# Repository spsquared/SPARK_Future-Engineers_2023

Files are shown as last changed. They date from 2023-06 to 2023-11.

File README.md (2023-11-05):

<div align=center>

banner

</div>

***

**Official GitHub repository for WRO USA Future Engineers team SPARK 2023. All code, documentation, and files are located here.**

***

# Contents
* [**Hardware Design**](#hardware-design)
    * [Chassis](#chassis)
    * [Power & Control](#power--control)
    * [Motors](#motors)
    * [Sensors](#sensors)
    * [Wiring Diagram](#wiring-diagram)
* [**Software Design**](#software-design)
* [**Photos**](#photos)
* [**In-depth Algorithm Documentation**](ALGORITHM.md)
* [**Build & Setup**](#build--setup)
    * [Parts List](#parts-list)
    * [Important Assembly Notes](#important-assembly-notes)
    * [Jetson Nano Setup](#jetson-nano-setup)
        * [General Information](#general-jetson-nano-information)
        * [OS Installation](#os-installation)
        * [SSHFS & Static IP](#sshfs--static-ip)
        * [GPIO & I2C](#enable-gpio-and-i2c)
        * [Package Installation](#package-installation)
        * [Camera Profile Fix](#camera-profile-fix)
        * [Calibration](#calibration)
        * [Running Programs](#running-programs)
* [**Demonstration Videos**](#demonstration-videos)
* [**Team Photos**](#team-photos)
* [**SPARK Utilities**](#spark-utilities)
    * [SPARK Control Panel](#spark-control-panel)
        * [Map View](#map-view)
        * [Changing Parameters](#changing-parameters)
    * [SPARK Randomizer](#spark-randomizer)
    * [Setup](#spark-utility-setup)
* [**Lessons Learned**](#lessons-learned)
* [**LiPo Battery Safety Notice**](#lipo-battery-safety-notice)

***

# Hardware Design

SPARK G2 consists of a 3D-printed chassis with off-the-shelf components mounted to it, like motors, cameras, and controller boards. For a full component list, see [SETUP.md](./SETUP.md#parts-list). CAD models can be found in `/dist/3d-models/`, and have all been [modeled in Onshape here](https://cad.onshape.com/documents/82dd14d30b814e8846567203/w/34e1b6a4058ed5fbde8ef66a/e/47aa4028e09ec17a24a63590).

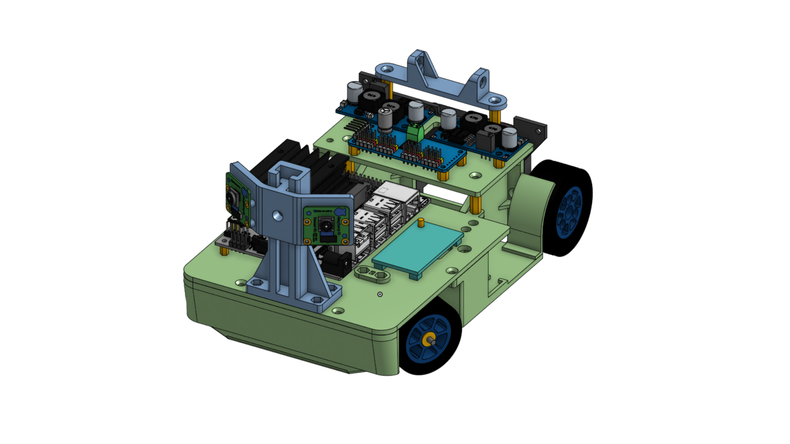
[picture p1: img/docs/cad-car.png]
SPARK G2 chassis with electronics in CAD software


***

## Chassis

The chassis consists of a lower base with vertical walls to mount the rear axle and upper platforms. It has space for the battery and ESC (electronic speed controller) bay in the rear, and a compartment in the front for the steering mechanism. The rear axle is sourced from the Atom 2 GT12 pan car kit by Schumacher and is mounted vertically to save space.

The electronics platforms sit on top of the chassis base, and the main platform is also a structural component that provides rigidity to the chassis. Because the electronics are on top, they are easily accessible and wiring is fairly simple. The only exceptions are the ESC, which is in the rear, and the IMU (inertial measurement unit, used for measuring angles and velocity).

| Chassis base with rear axle and steering | Chassis base and platforms, without camera tower |
| --- | --- |
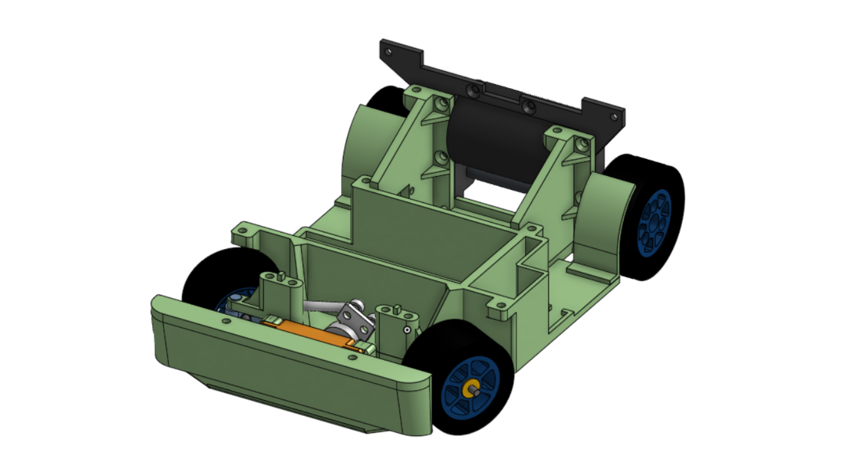
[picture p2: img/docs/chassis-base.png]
Lower chassis base
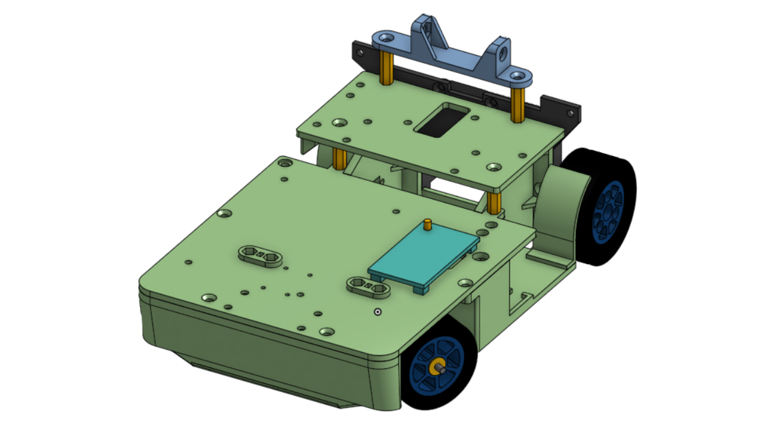
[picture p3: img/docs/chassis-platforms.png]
Chassis with platforms
|  |  |

The wheels are made of 3D-printed rims with LEGO tires, and the front steering linkage is a custom design with an exaggerated [Ackerman steering geometry](https://en.wikipedia.org/wiki/Ackermann_steering_geometry). (This can be seen in the [Motors section](#motors))

## Power & Control

The vehicle power is supplied by a single 3s LiPo battery, running at 12 Volts. This 12V power is run into three components in parallel: The ESC, 5V regulator, and 7.4V regulator. The regulators ensure that the Jetson Nano and servo do not get damaged from overvoltage, and the ESC can run directly off of the main 12V line.

The Jetson Nano uses an intermediate PWM control board to control the drive and steering motors. The control board and Nano communicate through I2C, and that is converted to a PWM signal for the motors to interpret. The drive motor has an additional speed controller.

| Top-down view of SPARK G2 in Onshape | Individual components |
| --- | --- |
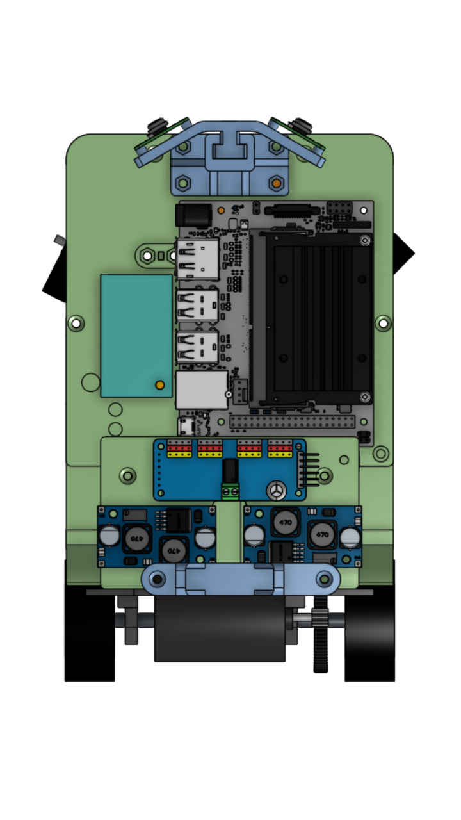
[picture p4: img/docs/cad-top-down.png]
Top-down in CAD
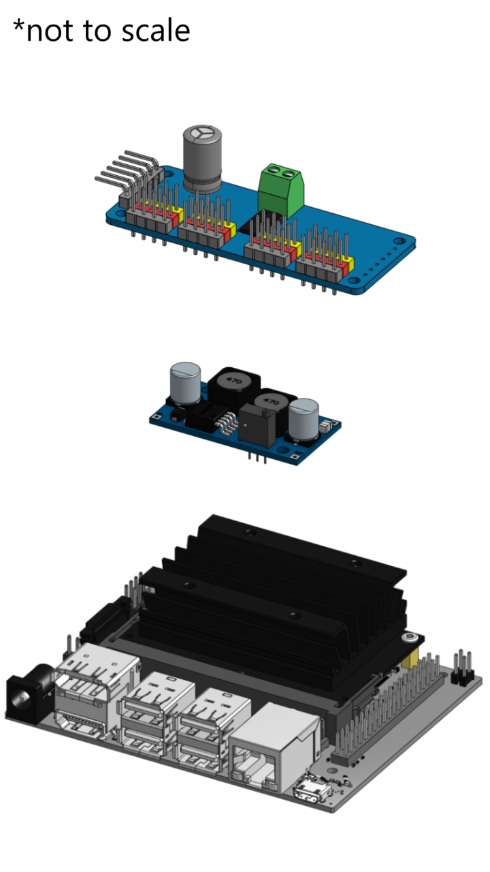
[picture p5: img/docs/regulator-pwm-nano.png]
Individual components
|  |  |
| Front of vehicle at top | (top-to-bottom) - PWM Driver, Voltage regulator, Jetson Nano |

## Motors

SPARK is rear-wheel drive, with a sensored brushless drive motor and high-quality servo from Savox. The drive motor is controlled by the brushless ESC (electronic speed controller) and has a sensor. Brushless motors allow for finer control at low speeds, and the addition of a sensor helps too.

It still would be better to use a lower kV motor (a slower motor) with an [ODrive](https://odriverobotics.com/) and encoder for even better low-speed control, but the current setup is sufficient.

We chose to use the Savox SV1260MG for our steering servo because of its speed - with transit times of under 100ms, this servo would not limit our control of the vehicle. It can also run at higher voltages, meaning we can get more power out of it.

| Drive motor | Servo and steering |
| --- | --- |
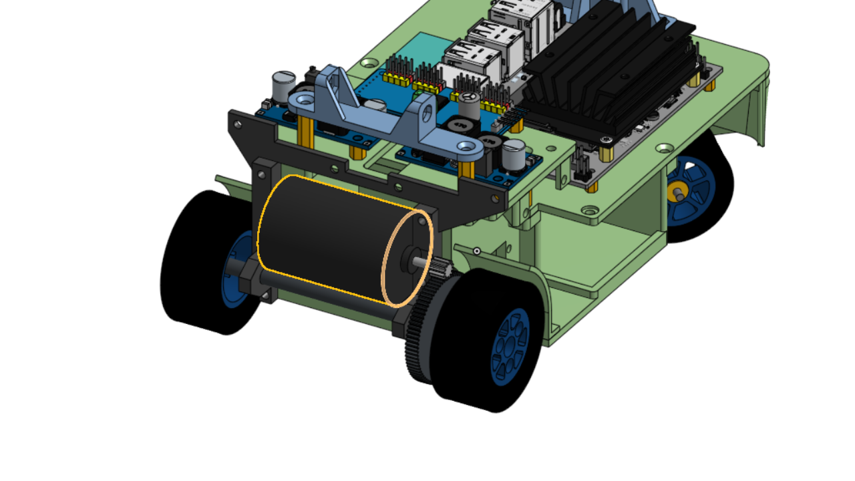
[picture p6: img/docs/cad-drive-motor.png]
Drive motor
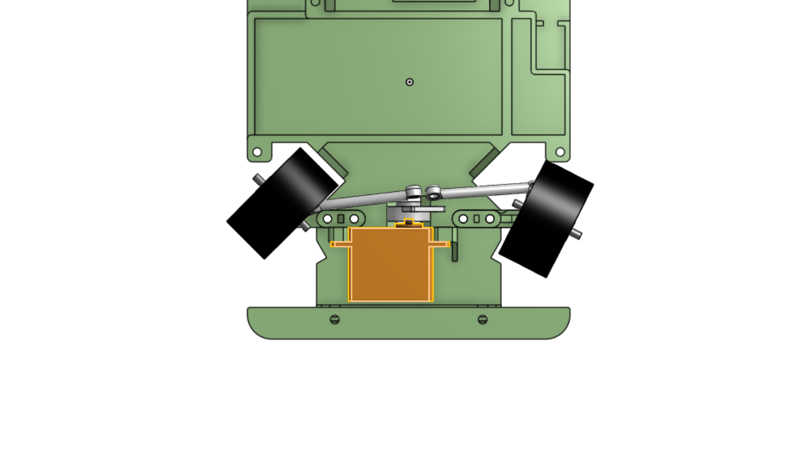
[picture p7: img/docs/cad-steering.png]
Servo and steering mechanism
|  |  |

## Sensors

One major physical change is the addition of a second IMX219 wide-angle camera to the front of the car. Both cameras are angled 30 degrees to either side, with a field of view of 150 degrees for each camera. The cameras are mounted on a slider to ensure the accuracy of the [distance calculations in the algorithm](./ALGORITHM.md#merge-contours--wall-lines).

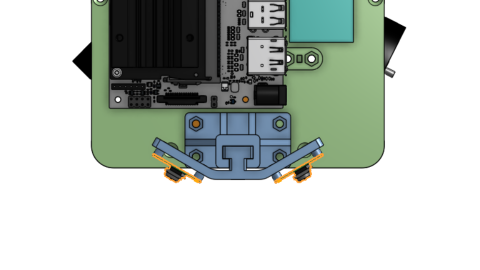
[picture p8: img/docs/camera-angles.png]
Cameras top-down


In addition to the two wide-angle cameras, SPARK G2 has an IMU (inertial measurement unit) for measuring the angle of the vehicle. It also has the capability to measure linear acceleration, but we don't use that. It communicates over I2C directly with the Jetson Nano.

SPARK G2 does not use any other sensors to perceive its environment - no LiDAR here!

## Wiring Diagram

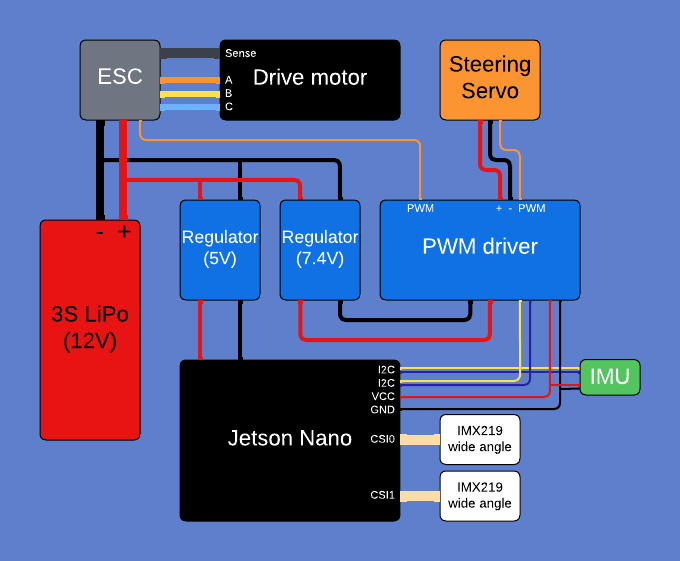
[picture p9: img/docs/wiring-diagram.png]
Wiring diagram


***

# Software Design

[**For a detailed explaination of the SPARK G2 algorithms, see Algorithm.md!**](ALGORITHM.md)

## [Obstacle Management Algorithm](ALGORITHM.md)

* [**Image Processing**](ALGORITHM.md#image-processing)
    1. [Crop the image](ALGORITHM.md#crop-the-image)
    2. [Undistort](ALGORITHM.md#undistorting)
    3. [Filter](ALGORITHM.md#filtering)
    4. [Find wall heights](ALGORITHM.md#finding-wall-heights)
    5. [Find contours](ALGORITHM.md#finding-contours)
    6. [Find wall lines](ALGORITHM.md#finding-wall-lines)
    7. [Merge & Convert wall lines and contours](ALGORITHM.md#merge-contours--wall-lines)
    8. [Categorize Walls](ALGORITHM.md#categorizing-walls)
    9. [Find Car Orientation](ALGORITHM.md#finding-car-orientation)
    10. [Filter Traffic Signals/Obstacles/Pillars/Game Objects](ALGORITHM.md#filtering-traffic-signals)
* [**Steering and Motion Planning**](ALGORITHM.md#steering-and-motion-planning)
    1. [Find Lap Direction](ALGORITHM.md#finding-lap-direction)
    2. [Calculate Steering](ALGORITHM.md#calculating-steering)

## Pseudo Code

The algorithm part of the code is a loop. Each iteration, it takes images, processes them, and then calculates a steering value.

Each iteration takes about 80ms.

```
while (sections entered != 24): # 24 sections means 3 laps.
    // Image processing for car localization
    Crop the images
    Undistort the images (how to add links to other files?)
    Filter the image
    Find wall heights
    Find contours
    Find wall lines
    Merge and Convert wall lines and contours
    Categorize Walls
    Find Car Orientation
    Filter Pillars
    <!--Car steering control-->
    Find lap direction
    Calculate Steering
```

***

# Photos

*(Click to view detail)*

| | |
| --- | --- |
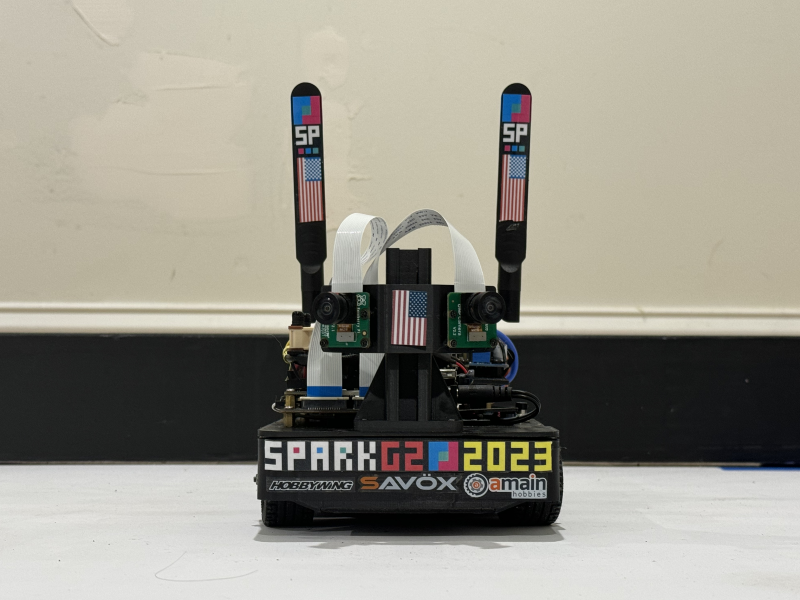
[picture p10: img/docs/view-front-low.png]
Front view
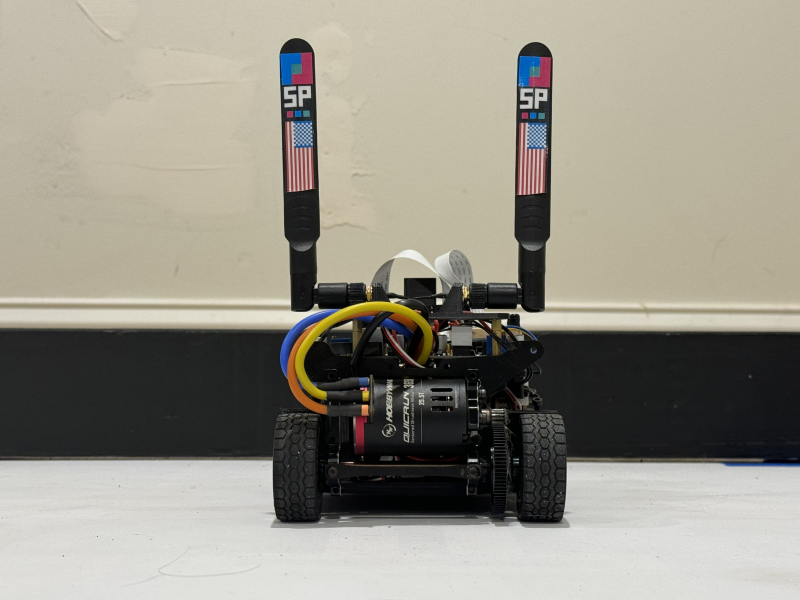
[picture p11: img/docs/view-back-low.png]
Back view
|  |  |
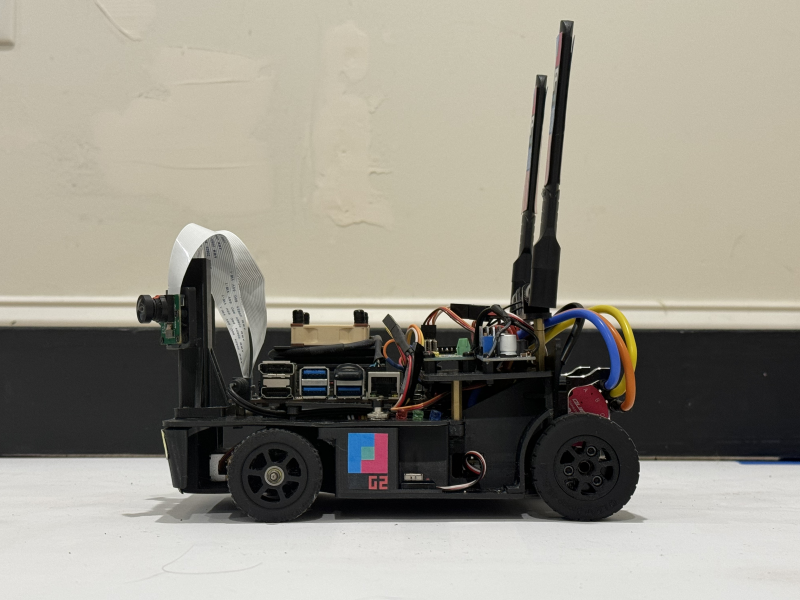
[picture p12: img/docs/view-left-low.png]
Side left view
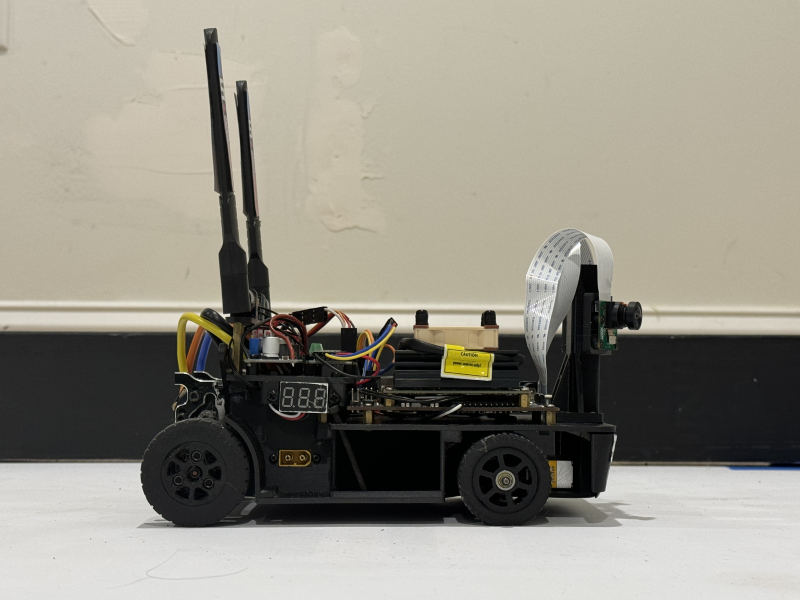
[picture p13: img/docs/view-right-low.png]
Side Right view
|  |  |
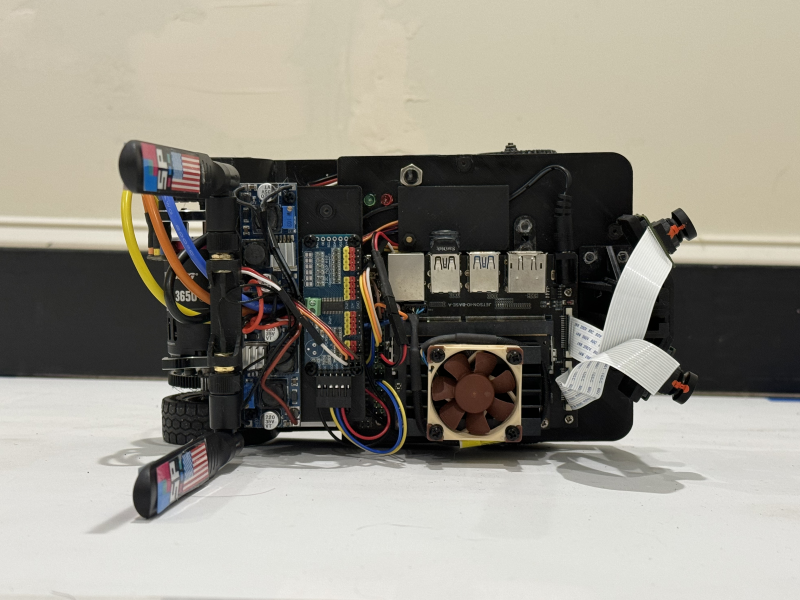
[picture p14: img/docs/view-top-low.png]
Top view
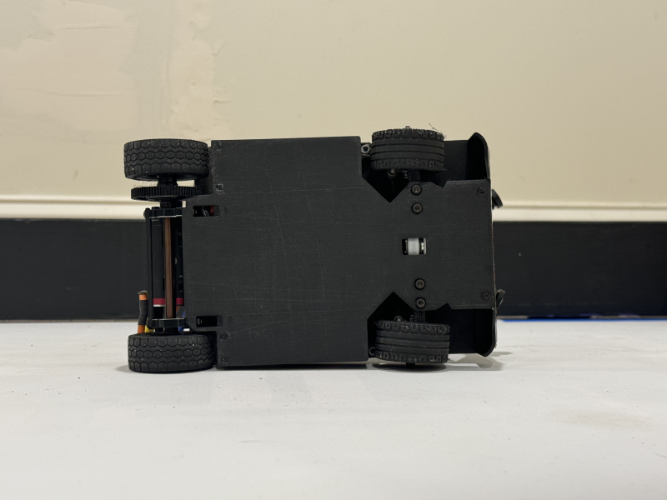
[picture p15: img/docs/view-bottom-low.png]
Bottom view
|  |  |

***

# Demonstration Videos

| Open Challenge | Obstacle Challenge (no U-turn) | Obstacle Challenge (U-turn) |
| --- | --- | --- |
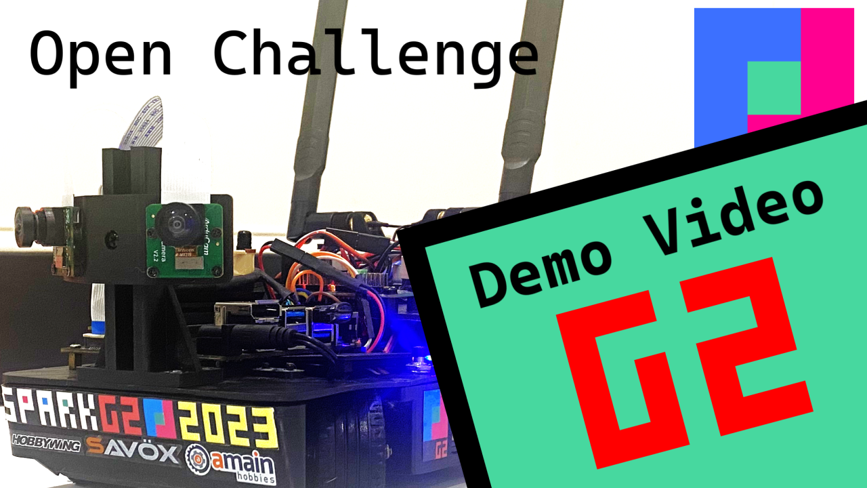
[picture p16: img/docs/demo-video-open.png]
SPARK WRO Future Engineers 2023 Internationals Demonstration Run - Open Challenge (https://youtu.be/1Tk8J1Zt5vI)
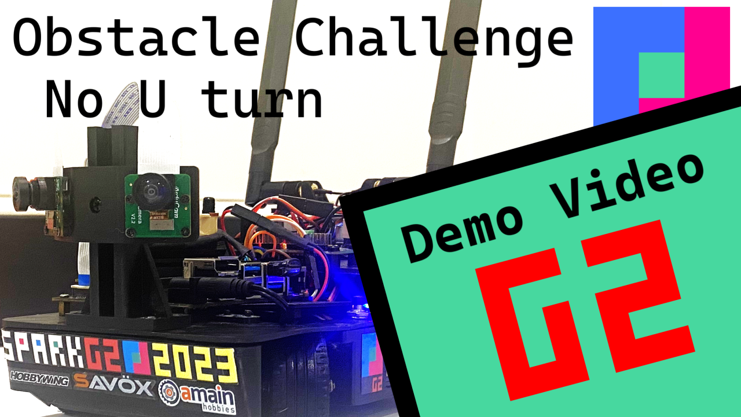
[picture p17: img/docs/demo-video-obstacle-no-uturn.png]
SPARK WRO Future Engineers 2023 Internationals Demonstration Run - Obstacle Challenge - No U turn (https://youtu.be/DUGlUvpnOEw)
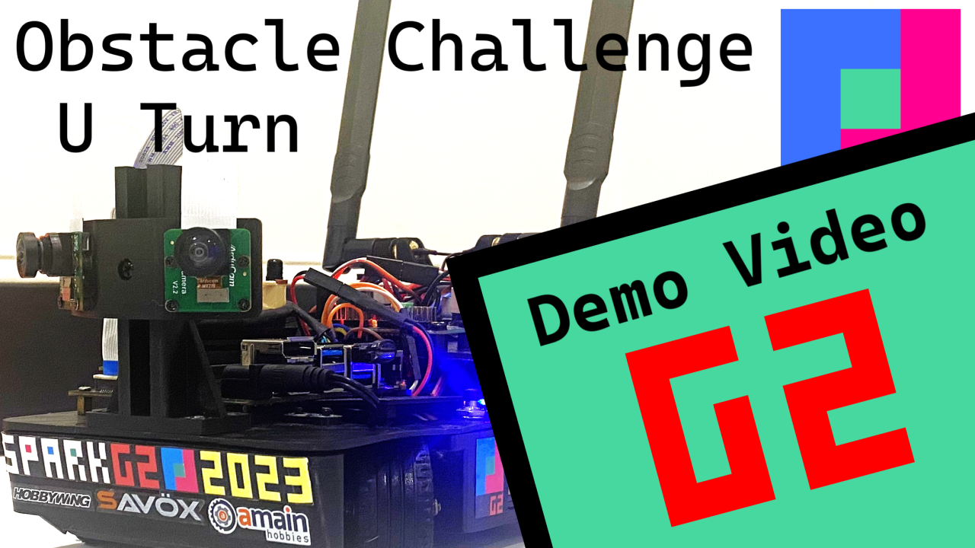
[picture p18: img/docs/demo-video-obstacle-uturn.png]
SPARK WRO Future Engineers 2023 Internationals Demonstration Run - Obstacle Challenge - U turn (https://youtu.be/UDNGXfyl8ww)
|  |  |  |

***

# Build & Setup

**This section is a walkthrough of the build process and setup of the controller, a Jetson Nano.**

***

You will need (at least) the following tools:
* 3D printer or access to 3D printing service
* Hex Allen drivers (key or bits)
* Phillips head drivers
* Crimping kit
* Soldering iron

***

## Parts:

* At least 0.8kg PLA filament
* Parts from [Schumacher Atom 2 S2 1/12 GT12 Competition Pan Car Kit](https://www.amainhobbies.com/schumacher-atom-2-s2-1-12-gt12-competition-pan-car-kit-schk179/p1055346) (not sponsored)
    * [Drive Pod Parts](https://www.racing-cars.com/gt12/atom-2/atom-2-parts=chassis-parts/s2-pod-parts-atom-2-u7905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)
    * [Assembled Differential](https://www.racing-cars.com/gt12/atom-2/atom-2-parts=transmission/assembled-diff-atom-2-u7713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)
    * [Left Drive Wheel Clamp](https://www.racing-cars.com/gt12/atom-2/atom-2-parts=transmission/lh-drive-clamp-a1-a2-u4853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)
    * Transmission Housings: [Left Side](https://www.racing-cars.com/gt12/atom-2/atom-2-parts=transmission/trans-housing-lh-a2-3-e2-e5-u7483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), [Right Side](https://www.racing-cars.com/gt12/atom-2/atom-2-parts=transmission/trans-housing-rh-a2-3-e2-e3-e4-u7484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)
    * [Ride Height Adjusters](https://www.racing-cars.com/gt12/atom-2/atom-2-parts=suspension/ride-height-adjusters-0-25-1-75-4prs-e1-5-ic-2-a3-u4973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) (use 1.75mm)
    * 2x [LP Front Axle](https://www.racing-cars.com/gt12/atom-2/atom-2-parts=suspension/low-profile-front-axle-a1-a3-u7302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)
    * [Rear Axle Ball Bearings](https://www.racing-cars.com/gt12/atom-2/ball-bearing-1-4x3-8x1-8-flanged-yellow-pr-u4980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)
    * [Front Axle Ball Bearings](https://www.racing-cars.com/gt12/atom-2/ball-bearing-1-8x5-16-flanged-yellow-pr-u4981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)
    * [Steel shims](https://www.racing-cars.com/gt12/atom-2/s-steel-shims-1-4x5-16x0-004-ss-at-ecl-u4112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)
    * [M3 Nyloc Nuts](https://www.racing-cars.com/gt12/atom-2/m3-alloy-nyloc-nuts-low-profile-black-pk10-cr517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)
    * [Servo Horn](https://www.racing-cars.com/gt12/atom-2/atom-2-parts=chassis-parts/25t-servo-saver-assembly-a2-e3-e4-u7895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)
    * [Ball Studs (short)](https://www.racing-cars.com/gt12/atom-2/pro-ball-stud-short-pk4-u4274?returnurl=%2fgt12%2fatom-2%2f)
* [Yahboom Jetson Nano 4GB Developer Kit](https://category.yahboom.net/collections/jetson/products/jetson-nano-sub)
* 2x [Arducam Raspberry Pi Official Camera Module V2, with 8 Megapixel IMX219 Wide Angle 175 Degree Replacement](https://www.amazon.com/Arducam-Raspberry-Official-Megapixel-Replacement/dp/B083PW4BLH/)
* [Intel AX201 WiFi 6 BT 5.1 M.2 2230 with 10in RP-SMA Antenna](https://www.newegg.com/p/0XM-009Y-001C7) (not required but helpful)
* [Noctua NF-A4x10 5V](https://noctua.at/en/products/fan/nf-a4x10-5v) (not required)
* [Adafruit MPU-6050 6-DoF Accelerometer & Gyroscope Sensor (with STEMMA QT connector)](https://www.adafruit.com/product/3886)
* [PCA9685 16 Channel PWM Driver](https://www.amazon.com/HiLetgo-PCA9685-Channel-12-Bit-Arduino/dp/B01D1D0CX2)
* [HobbyWing QUICRUN 10BL60 Brushless ESC Sensored](https://www.hobbywingdirect.com/products/quicrun-10-sensored)
* [HobbyWing QUICRUN 3650 Sensored Brushless Motor G2 (25.5T)](https://www.hobbywingdirect.com/collections/quicrun-brushless-motor-series-sensorless/products/quicrun-3650-sensored-2-pole-brushless-motor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)
* [Savox SV1260MG Digital Mini Servo](https://www.savoxusa.com/products/savsv1260mg-mini-digital-high-voltage)
* A LiPo balance charger with XT-60 connector, rated for 3S
* [Zeee Premium Series 3S LiPo Battery 4200mAh 11.4V 120C with XT60 Plug](https://www.amazon.com/Zeee-Premium-Compatible-Helicopter-Airplane/dp/B09CMLSK67)
* 2x [XL4015E1 DC-DC 5A Adjustable Buck Converter](https://www.amazon.com/Adjustable-Converter-1-25-36v-Efficiency-Regulator/dp/B079N9BFZC)
* [DC Digital Voltometer](https://www.amazon.com/bayite-Digital-Voltmeter-Display-Motorcycle/dp/B00YALUXH0/)
* [Male 5.5mm DC Barrel Connectors](https://www.amazon.com/Pigtails-Female-Connector-Pigtail-Security/dp/B08PYWN3T7/)
* [Panel-Mountable Female XT60 Connectors](https://www.amazon.com/XT60E-M-Mountable-Connector-Models-Multicopter/dp/B07YJMCDC3)
* [Normally Closed/Momentary On Push Button](https://www.amazon.com/Pieces-normally-closed-Button-Momentary/dp/B07HCLVMGS/) (size must match)
* [12 Tooth 48 Pitch Pinion Gear with Set Screw](https://www.amazon.com/Traxxas-PINION-PITCH-SCREW-2428/dp/B00EFXMUO2)
* [78 Tooth Spur Gear 48 Pitch](https://www.amazon.com/Kimbrough-Pitch-Spur-Gear-78T/dp/B0006O1QVM)
* 16, 20 gauge wire
* M3 nylon screws (6mm)
* M3 nylon standoffs (6mm works best)
* M3 nylon nuts
* M3 nuts
* Countersunk, cap head M3 screws (6mm and 8mm work best)
* Socket cap head M3x40mm screws [(like these)](https://www.amazon.com/Alloy-Steel-Socket-Screws-Black/dp/B00W97R5KU)
* Differential lubrication

## Important Assembly Notes

If you need a reference model we have our [OnShape document linked](https://cad.onshape.com/documents/82dd14d30b814e8846567203/w/34e1b6a4058ed5fbde8ef66a/e/47aa4028e09ec17a24a63590). (The ESC and IMU have not been modeled. The ESC goes in the rear, within the raised rectangle. The IMU should be mounted to the 4 unpopulated holes with M2.5 screws.)

### [**We HIGHLY recommend that you visit this document!**](https://cad.onshape.com/documents/82dd14d30b814e8846567203/w/34e1b6a4058ed5fbde8ef66a/e/47aa4028e09ec17a24a63590)

Follow the diagram below to wire the button and indicator LEDs. *(Click to view detail)*

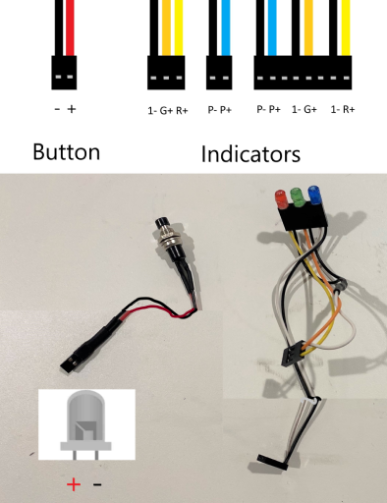
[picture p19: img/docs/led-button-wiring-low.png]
Button and indicator LED wiring


*Note: For I2C connectors, Yellow should be SCL, and blue should be SDA; there is no set standard.*

For soldering, we recommend soldering the regulators to their own connectors **in parallel**, and using that as a pass-through to the ESC. The female connectors should be used on the ESC inputs and regulator input, and the male connector on the pass-through end of the regulator wires. See the diagram below.

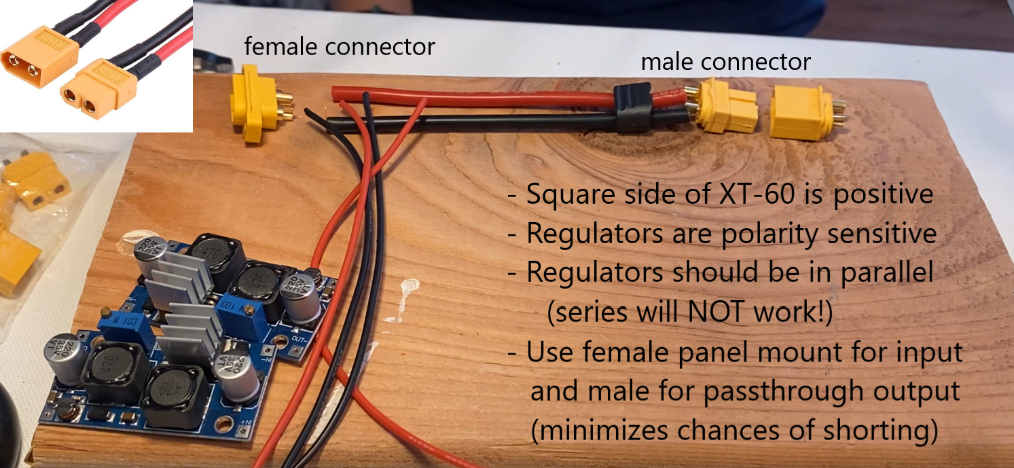
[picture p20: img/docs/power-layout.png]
Wiring for regulator passthrough


Follow the quick start guide for the ESC to solder the motor connections. Summary: solder A, B, and C connectors to the motor (or supplied connectors). Ensure the sensor wire is secure before mounting the motor and ESC.

**WARNING:** DO NOT CONNECT THE ESC 3-PIN DIRECTLY TO THE SERVO DRIVER! IT WILL BACKDRIVE THE REGULATOR AND BREAK IT! ONLY CONNECT THE PWM PIN (white)!

The images below show the correct pins on the Jetson Nano to plug the connectors onto. **Always double-check your connectors!**

 *(Click to view detail)*

| Pinout sheet | Jetson Nano | PWM driver |
| --- | --- | --- |
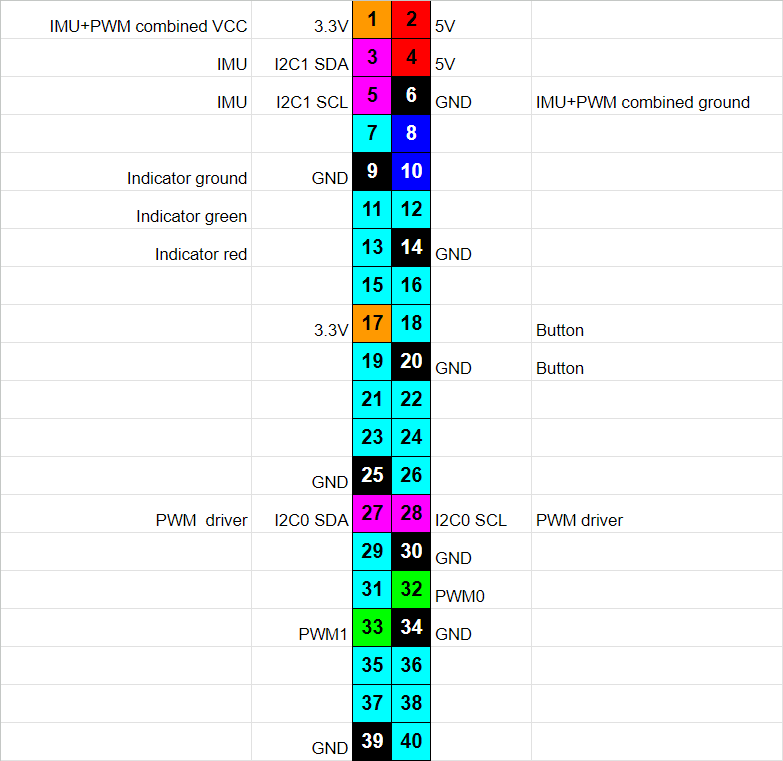
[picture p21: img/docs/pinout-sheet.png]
Pinout screenshot (https://docs.google.com/spreadsheets/d/1WAe1DtCbWhLoC4L6yzJYvS99iHG4yAiWakqxsy8os7s/edit?usp=sharing)
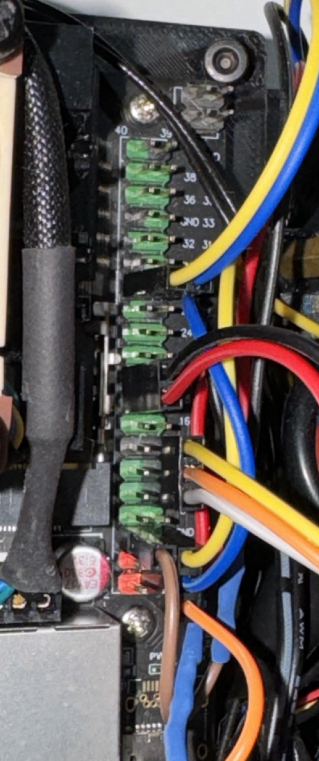
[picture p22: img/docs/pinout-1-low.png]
Connectors on Jetson Nano
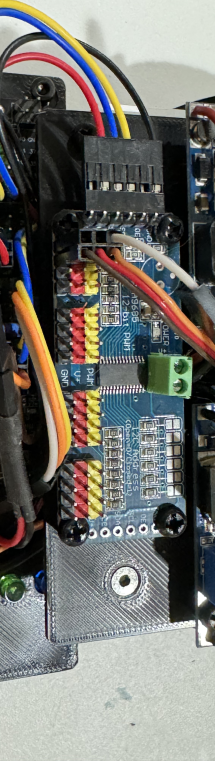
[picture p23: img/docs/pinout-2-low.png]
Connectors on PWM driver
|  |  |  |

## Jetson Nano Setup

**This section is a walkthrough of the software environment setup.**

### General Jetson Nano Information

SPARK G2 is designed to run on a Jetson Nano with Ubuntu 18.04, with the Jetpack SDK installed. This means that Python should already be installed. The program is mainly written in Python, with some code in JavaScript for the SPARK Utilities.

Here are the most important subsections in this section:
* [General Information](#general-jetson-nano-information)
* [OS Installation](#os-installation)
* [Package Installation](#package-installation)
* [Running Programs](#running-programs)

### OS Installation

Visit [Yahboom](http://www.yahboom.net/)'s [setup and tutorial repository](http://www.yahboom.net/study/jetson-nano) to begin setting up the [Jetson Nano 4GB](https://category.yahboom.net/collections/jetson/products/jetson-nano-sub). Follow steps 1.1-1.7 in "Development setup > SUB Version".

> http://www.yahboom.net/study/jetson-nano <!-- not the right way to use markdown quotes but oh well -->

This guide should install the default Ubuntu 18.04 with Jetpack SDK, with Python 3.6 pre-installed.

***

### SSHFS & Static IP

After setting up the board, follow step 2.1 in the "Basic Settings" section to log into your Jetson Nano. **Keep PuTTY open**, as it will be used for the rest of the setup process. **Also keep the IP**.

Make sure a **static IP is set** to the board to make SSH and file transfer easier. Go to your router settings and [assign a DHCP reservation (PCmag)](https://www.pcmag.com/how-to/how-to-set-up-a-static-ip-address) (or a straight static IP) to your Jetson Nano. **Save this IP** in your PuTTY settings and SSHFS mounting.

For remote file transfer, install sshfs (Linux only), or use [sshfs-win](https://github.com/winfsp/sshfs-win) from WinFsp. Follow instructions to mount the Jetson Nano to a network drive. Now upload all contents of the `/Program/` folder into a new folder on the Jetson Nano. **Remember the directory of the folder**, this will be used later.

***This method should be used to upload programs.***

**The *entire* `Program` directory must be uploaded for the program to run. Ensure the `path` constant in `startup.py` is defined properly.**

***

### Enable GPIO and I2C

Enable GPIO and I2C, create a new user group, and add your user to it.

```
sudo groupadd -f -r gpio
sudo usermod -a -G gpio your_user_name
```

Copy `99-gpio.rules` from `/dist/` in the project folder to `/etc/udev/rules.d/` on the Jetson Nano. Then enable the rule.

```
sudo udevadm control --reload-rules && sudo udevadm trigger
```

You may need to enable permissions for I2C

```
sudo usermod -a -G i2c your_user_name
```

**Reboot the Nano to apply changes.**

***

### Text-Only, Auto-Login, & Run on Startup

Switch the Jetson Nano to text-only mode (A GUI is almost useless for this application and only causes unnecessary slowness).

```
sudo systemctl set-default multi-user.target
```

Autologin must be done to avoid having to plug in a monitor and keyboard to start ssh and run programs. The following accomplishes it:

```
sudo systemctl edit getty@tty1
```

A temporary editor will appear. Place the following text in it, replacing "your_user_name" with your user name.

```
[Service]
ExecStart=
ExecStart=-/sbin/agetty -o '-p -f your_user_name' -a your_user_name --noclear %I $TERM
```

Save and close the editor with `:wqa`.

To run the program on startup, first obtain the directory of the program folder uploaded earlier. Create `spark_startup.service` in `/etc/systemd/system` and place the following in the contents, replacing "/filepath/" with the absolute directory of the folder (begins with a "/").

```
[Service]
WorkingDirectory=/filepath
ExecStart=/usr/bin/python3 -u /filepath/startup.py
User=username

[Install]
WantedBy=multi-user.target
```

Save the file and add permissions to it.

```
sudo chmod 644 /etc/systemd/system/spark_startup.service
systemctl enable /etc/systemd/system/spark_startup.service
```

If you wish to use the SPARK Control Panel, repeat the above steps to create a second startup service (`spark_server.service`). (Be sure to also install Node.js per the [package installation section](#package-installation)!) The contents should look like the below:

```
[Service]
WorkingDirectory=/filepath
ExecStart=/usr/bin/node /filepath/Util/server.js
User=username

[Install]
WantedBy=multi-user.target
```

Make sure to add the same permissions as `spark_startup.service`.

Reboot the Jetson Nano to test if these changes worked. No GUI should appear and you should be automatically logged in.

Enable run-on-startup by editing `run-on-startup.txt` in the folder. Replace the first line with `true`.

Go to `startup.py`, and change `path` to the absolute filepath of your directory (same as filepath in the previous steps)

Example:

```
path = '/home/nano/Documents/SPARK_FutureEngineers_2023/'
```

**Reboot the Jetson Nano again.**

***

### Package Installation

Some packages will need to be installed. [Jetson-GPIO](https://github.com/NVIDIA/jetson-gpio), socket.io-client, [adafruit-servokit](https://github.com/adafruit/Adafruit_CircuitPython_ServoKit), and [adafruit-mpu6050](https://github.com/adafruit/Adafruit_MPU6050) must be installed (Jetson-GPIO may be pre-installed on some versions). Additionally, [cv2](https://pypi.org/project/opencv-python/), an integral part of many robotics programs, must be installed.

Use the following pip command:

```
pip3 install adafruit-circuitpython-servokit adafruit-mpu6050 "python-socketio[client]" opencv-python
```

*Note: This may take a while.*

Additionally, [Node.js](https://nodejs.org/) should be installed to use the SPARK Control Panel. *We highly recommend this is done!*

```
sudo apt install nodejs
```

*NOTE: The default installation of Node.js may be v12, which doesn't support some features. To install newer versions, try the following:*

```
sudo snap install node --channel=16 --classic
sudo update-alternatives --install /usr/bin/node node /snap/bin/node 0
```

*This should install Node.js v16 and set it to be the main version of Node.js used with the "node" command.*

Navigate to `/Util/` and install dependencies.

```
npm install
```

***

### Camera Profile Fix

You may encounter pink fringing on the cameras. If that happens, take the following steps to fix it:

Copy `camera_overrides.isp` from `/dist/` in the project folder to `/var/nvidia/nvcam/settings/` on the Jetson Nano.

Give the override permissions with the next two:

```
sudo chmod 664 /var/nvidia/nvcam/settings/camera_overrides.isp
sudo chown root:root /var/nvidia/nvcam/settings/camera_overrides.isp
```

***

### Calibration

You need to calibrate the cameras for the undistortion to work properly. To do this, you need to take a couple of images of a chessboard using the SPARK Control Panel. Delete all the images in `/images`, and paste the images you took. Now, you need to run the first program of `calibrate.py`. This should print out the required D and K matrix. Now you can paste these matrices into the second program. Look in the `output` folder and check the images to make sure the undistortion is working. There should be some black gaps on the top and bottom of the image because undistorting the image stretches the corners. Make sure the lines on the chessboard are straight. Now you can paste the matrices into `converter.py` and it should work.

You also need to calibrate the wall heights. Run the Control Panel and start `manualdrive`. Now, open the SPARK-Calibrator and click Capture Image. Adjust the wall starts so that they are near the top of the wall. Paste the new values into `converter.py`.

***

### Running Programs

To run a program, connect to the vehicle using PuTTY and navigate to the `/Program/` folder. Then, use one of the following two commands to run a program.

```
python3 manualdrive.py
python3 autodrive.py
```

`manualdrive.py` is a testing program that **requires** the SPARK Control Panel - it will crash if SPARK Utilities are not set up! Once started, go to the [SPARK Control Panel](#spark-control-panel) and your computer will automatically connect to the vehicle if configured. For more information, see the [section on the Control Panel](#spark-control-panel).

`autodrive.py` is the competition program. It can be run with the SPARK Utility server for debugging, but during competitions, or when testing without the server, it can be run headless (without a user interface). Simply add the flag `no_server` to disable the server. **This is how the program is run during competitions**

```
python3 autodrive.py no_server
```

***

# Team Photos

| Team Photo | the other thing |
| --- | --- |
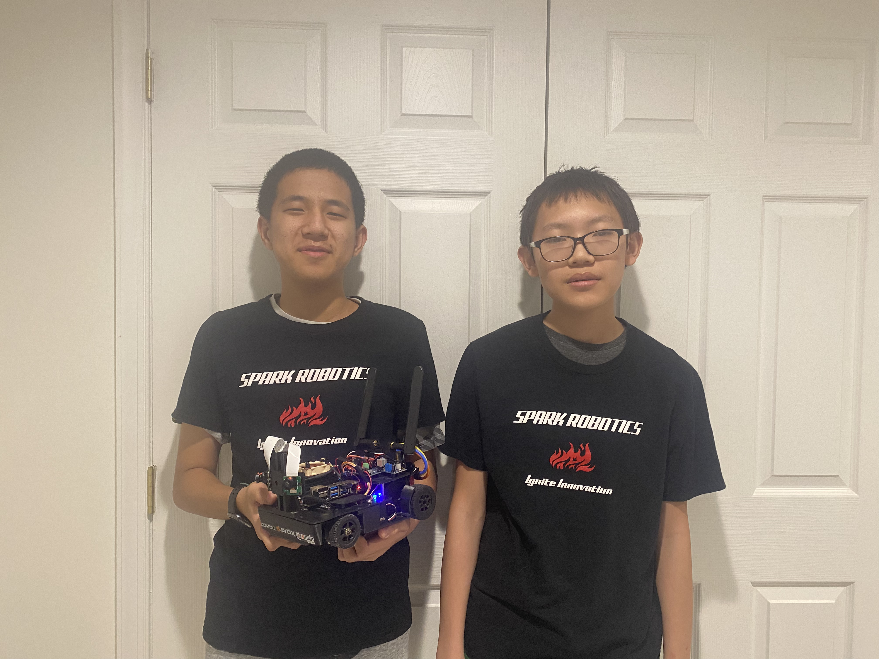
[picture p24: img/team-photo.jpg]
Team photo
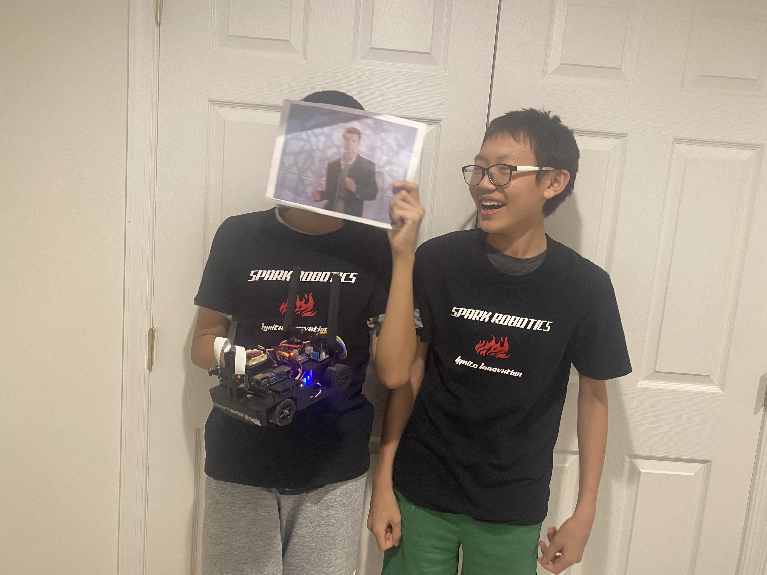
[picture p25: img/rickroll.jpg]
Rickroll
|  |  |

***

# SPARK Utilities

We (team SPARK) have created our own utilities to remotely command and monitor our robot from our computers. 

**This section covers installing and using these utilities.**

***

## SPARK Control Panel

SPARK Control Panel is our own testing and debugging software. It allows us to log detailed information about the program's internal workings and present it in a graphical format. SPARK Utilities work wirelessly, so as long as the network is configured correctly ([setup instructions](#spark-utility-setup)) the SPARK Control Panel can communicate with the robot.

<div align=center>

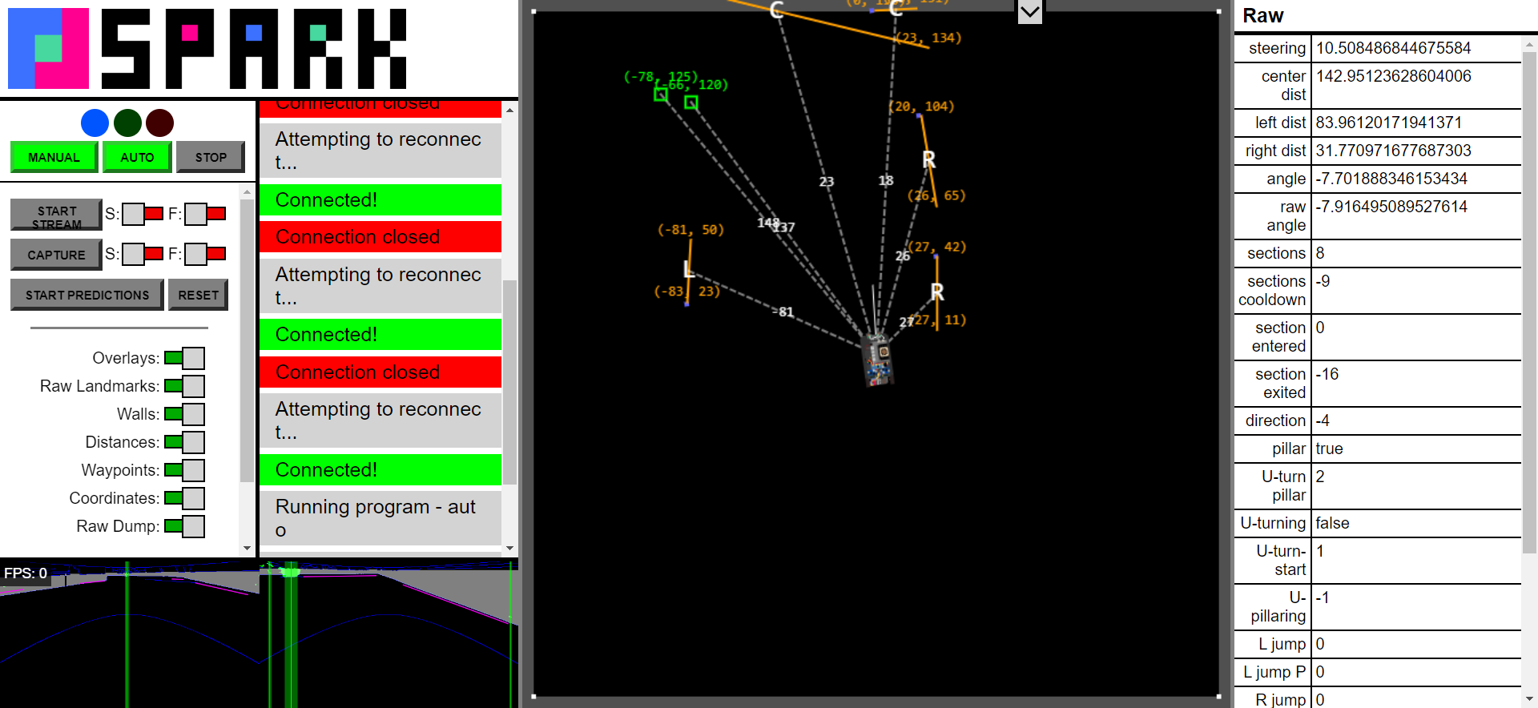
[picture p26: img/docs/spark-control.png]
SPARK Control Panel


</div>

On the left side of the screen, there are controls and camera views. There are buttons to run programs at the top, along with the indicator LEDS that reflect the ones on the vehicle.

Below that, there are camera controls. There are options to view and save image streams or individual images, with filtering enabled. A recent addition allows you to run the algorithm on frames from wherever.

At the bottom, there are options to toggle different displays on the Control Panel. Hover over them to get a description of their function.

There are also buttons to import and export sessions, as well as save a screenshot of the current frame from the cameras.

***

### Map View

The map on the right side of the screen is the most important addition to the SPARK Control Panel.

***

### Changing Parameters

It's possible to use SPARK Control to change the filter colors to adjust to the environment. Simply open the dropdown menu above the map on the right-hand side of the screen, change the HSV sliders, and click the "Capture" button with the "Filter" option enabled to see the effects of your changes. Afterwards, locate the color assignments in `/Program/Controller/converter.py` and change them to match your environment.

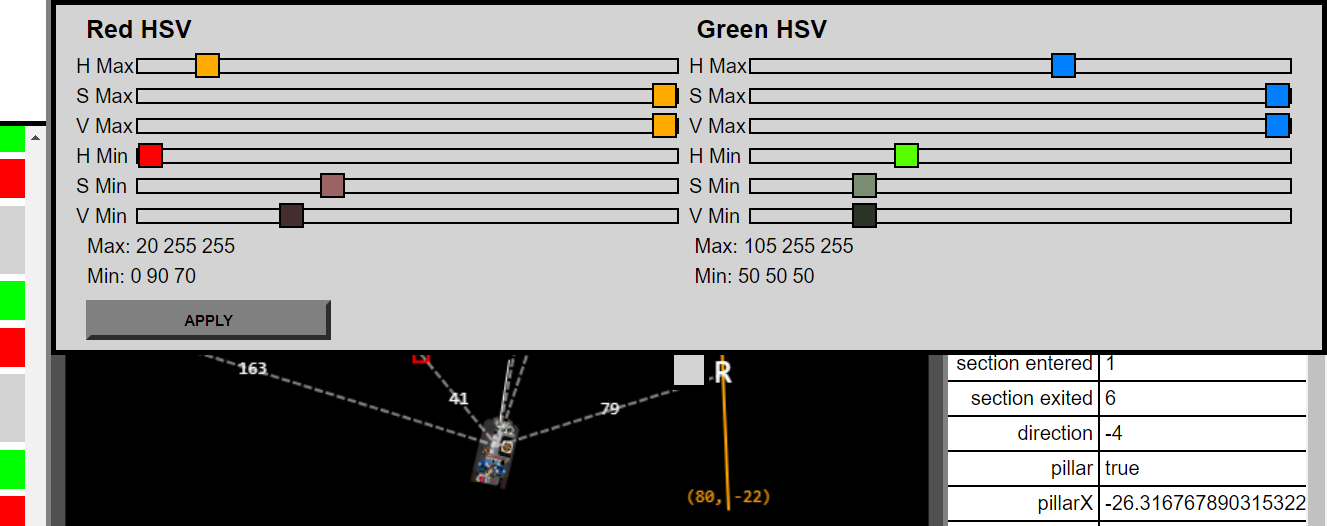
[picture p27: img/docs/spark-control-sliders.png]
HSV Sliders on control panel


Example:

```
rm = redMin = (0, 90, 70)
rM = redMax = (20, 255, 255)
gm = greenMin = (50, 50, 50)
gM = greenMax = (105, 255, 255)
```

You can update the defaults in `/SPARK-Control/index.js` as well in `initcolors`

Example:

```
const initcolors = [
    [
        [20, 255, 255],
        [0, 90, 70]
    ],
    [
        [105, 255, 255],
        [50, 50, 50]
    ],
];
```

**Don't forget to upload the `Program` folder again!**

***

## SPARK Randomizer

SPARK Randomizer is a tool to use when the card-drawing, coin-flipping, headache-inducing randomizing system is too slow. SPARK Randomizer generates valid cases (as long as the right button is clicked) according to the 2023 rules.

<div align=center>

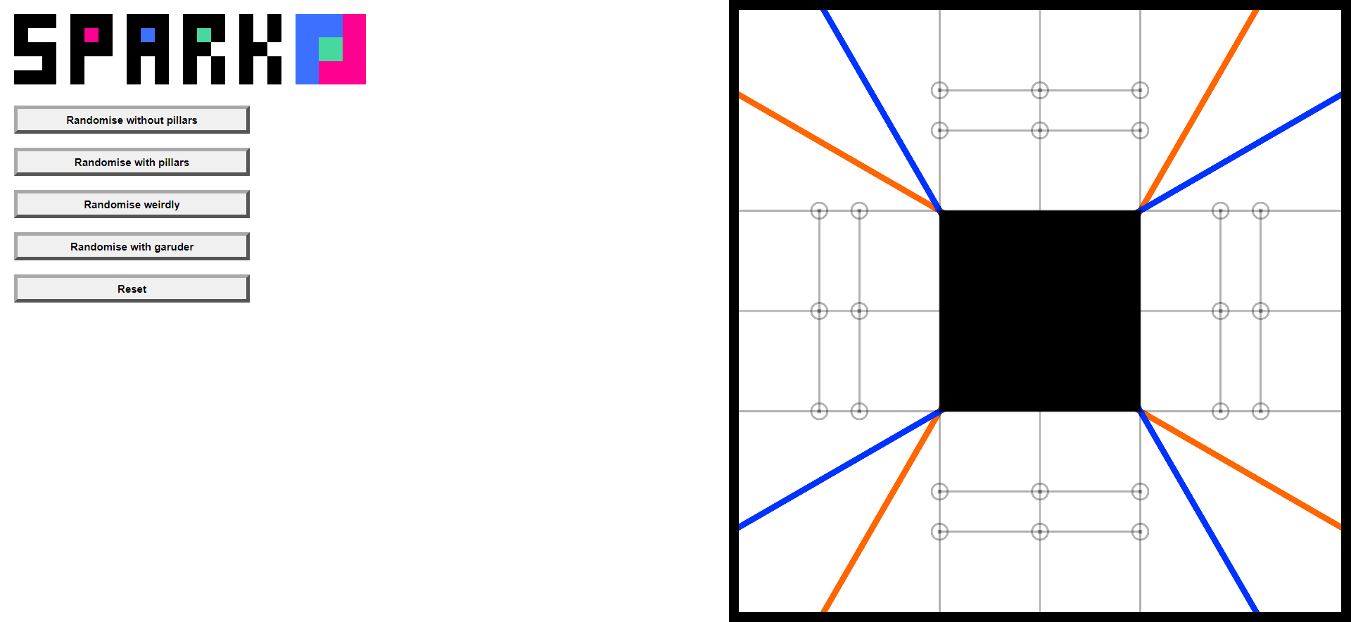
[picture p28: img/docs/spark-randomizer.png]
SPARK Randomizer


</div>

## SPARK Utility Setup

SPARK Utilities run on a separate Node.js process and are not necessary. If you want access to the SPARK Control Panel you must install Node.js and dependencies.

**See [the package installation section](#package-installation) to install Node.js.**

For the authentication system to work properly (not actual authentication, just a UUID exchange to prevent people from sending bogus signals) `auth.json` must be created in `/Util/`.

```
vim auth.json
```

The contents should be a single UUID:

```
"214e7634-b7c3-4044-b297-533da8cfbe7f"
```

This UUID should also be present on client devices, along with the IP of the car (set earlier). On the client devices, create `/SPARK-Util/SPARK-Control/config.js`.

Example:

```
const ip = '192.168.1.151';
const auth_uuid = '214e7634-b7c3-4044-b297-533da8cfbe7f';
```

To open the SPARK Control Panel and other utilities, run `node SPARK-Util/static.js` on a local terminal (your computer) or open the batch file `/SPARK-Util/static.bat`. In a web browser (only Chrome tested), navigate to `localhost:8081` to access the SPARK Control Panel.

***

# Lessons Learned

* We learned that you need to use `numpy` or `cv2` for almost all the image processing because python `for` loops are way too slow.
* We learned that simplicity is almost always better:
* We started by trying SLAM (Simultaneous Localization And Mapping) for our car, which turned out to be unnecessary for our purpose. So we instead switched to a simplified version, which keeps only a rough location and orientation of the vehicle. This turns out to be a good balance between speed and accuracy.
* We originally wanted to emulate a LiDAR using the cameras, generating a point cloud, and using SLAM and such, but directly undistorting the image instead of the points and using simpler image-based algorithms (like Hough lines) was easier and more efficient.
* We learned that sending too quickly oscillating inputs to the servo will cause it to stop responding, because of a built-in safety protection. We fixed this by adding input smoothing.
* We learned that keeping an XSS bug is not a good idea.

***

# LiPo Battery Safety Notice

While LiPo batteries are the safest form of portable, affordable, high-density energy storage, there are still precautions to be taken when working with them. Lithium is a highly volatile element and will react with the water vapor in the air if exposed to it.

1. **Do not** puncture, deform, short, or heat LiPo batteries above 26° C (80° F) (299.15 K)
2. Store and charge LiPos in a *fireproof container* **away** from flammable materials and water
3. **NEVER** charge a swollen or damaged battery (e.g. damaged leads, swelling of cells, puncture in wrapping)
4. **NEVER** leave a charging battery unattended
5. Only charge LiPo batteries with chargers *designed for LiPo batteries*
6. Dropping a battery can cause sufficient damage to rupture a cell and cause shorts
7. Overdischarging a LiPo battery can cause **permanent damage**

If a LiPo battery goes below its minimum voltage (stated in the manual included or 3.3v multiplied by the number of cells connected in series) it can cause **permanent internal damage**. This damage is not visible until after further use, when it can swell, or potentially burst and **cause a FIRE**.

**Read all safety notes and instructions included with LiPo batteries before use.**

### For a more detailed LiPo safety manual there is one on [Tenergy Power](https://power.tenergy.com/lipo-safety-warnings/)

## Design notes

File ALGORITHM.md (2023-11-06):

<div align=center>

banner

</div>

***

**This file covers the algorithm used for obstacle management.**

***

# Contents
* [**Overview**](#algorithm-overview)
    * [Pseudocode](#pseudocode)
    * [Outline](#outline)
* [**Image Processing**](#image-processing)
* [**Simple Driver**](#simple-driver)

***

# Algorithm Overview

This year we added a lot more motion planning to our algorithm. Our code processes the camera image and uses it to find the position of the walls relative to the car and the position of the pillars. Using this information, we can figure out where we are supposed to go next and steer accordingly.

The main consideration for our algorithm is to balance localization accuracy and speed. For localization accuracy, our target is to know which section we are in, and how far away the walls and pillars are. We need to know which section we are in to count how many laps we have completed and to know when to U-turn. We need to know how far away the car is from walls and pillars for collision avoidance.

For motion planning, our controller finds a waypoint based on the pillar position and wall position, and the car will steer toward the waypoint. The waypoint will be updated every iteration. For the U-turn, the car will turn around the first pillar in the section.

Our program runs a constant update loop. All controller code can be found in `./Program/Controller/`, and is divided into two main modules: The `converter`, which pre-process images; and the `controller`, which does some processing and steering and motion planning. We have `slam code but we don't use it because it's borken`.

## Pseudocode

The algorithm part of the code is a loop. For each iteration, it takes images, processes them, and then calculates a steering value.

Each iteration takes about 80ms.

```
while (sections entered != 24): # 24 sections means 3 laps.
    // Image processing for car localization
    Crop the images
    Undistort the images (how to add links to other files?)
    Filter the image
    Find wall heights
    Find contours
    Find wall lines
    Merge and Convert wall lines and contours
    Categorize Walls
    Find Car Orientation
    Filter Pillars
    <!--Car steering control-->
    Find lap direction
    Calculate Steering
```

## Outline
* [**Image Processing**](#image-processing)
    1. [Crop the image](#crop-the-image)
    2. [Undistort](#undistorting)
    3. [Filter](#filtering)
    4. [Find wall heights](#finding-wall-heights)
    5. [Find contours](#finding-contours)
    6. [Find wall lines](#finding-wall-lines)
    7. [Merge & Convert wall lines and contours](#merge-contours--wall-lines)
    8. [Categorize Walls](#categorizing-walls)
    9. [Find Car Orientation](#finding-car-orientation)
    10. [Filter Traffic Signals/Obstacles/Pillars/Game Objects](#filtering-traffic-signals)
* [**Steering and Motion Planning**](#steering-and-motion-planning)
    1. [Find Lap Direction](#finding-lap-direction)
    2. [Calculate Steering](#calculating-steering)

# Image Processing

Steps 1-7 for image processing are in `./Program/Controller/converter.py`.
Steps 8-10 for image processing are in `./Program/Controller/controller.py`.

***

### Crop the image

Because our camera is the same height as the top boundary of the walls, the top of the walls appears as a flat line in the image. We crop out along the top boundary of the wall. This reduces noise in the background, as well as speeding up our processing.

### Undistorting

Because we use a fisheye camera (wide angle), our cameras output a distorted image. This causes certain objects to appear closer than they actually are. Before we can process the image, we must undistort it.

At the start of the program, `cv2.fisheye.initUndistortRectifyMap` is used with precalculated distortion matrices to create the remaps. We used a checkerboard image to calculate the distortion matrices D and K. See [SETUP.md](./SETUP.md#) for instructions on how to get the distortion matrix.

The undistort function calls `cv2.remap` to use the precalculated remaps to undistort the image. We scaled up the matrix K to partially zoom out the image to prevent too much of the image from being cropped out.

We present a few examples to explain the processing steps. All the examples are from the left camera. The same calculations are done on the right camera.

| Raw Image | Undistorted Image |
| --- | --- |
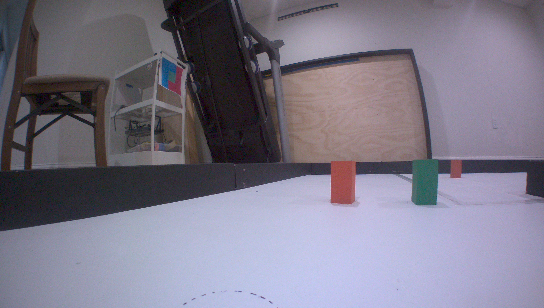
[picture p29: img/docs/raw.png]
raw IMAGE
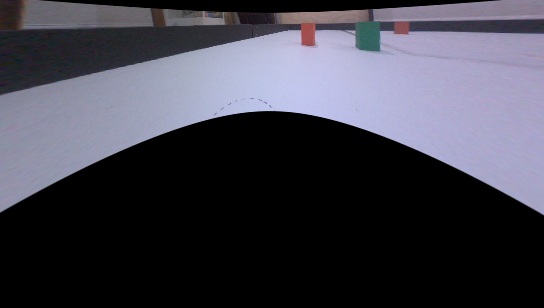
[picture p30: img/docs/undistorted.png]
cooked IMAGE
|  |  |

Because undistorting the image stretches out the edges, there are black gaps in the image on the top and bottom.

In the following image, the distortion is more obvious.

insert image

***

### Filtering

We filter the images to isolate the red pillars and green pillars. We also extract the edges of the walls in this step.

We found that it was easier and more robust to distinguish between very faint green colors and the wall when the image was in HSV mode. HSV stands for Hue-Saturation-Value. Hue is the "color" of the color, going from 0 to 179, covering the rainbow. Saturation is how much of the hue is present, going from 0 to 255, with lower values appearing duller. Value is how dark the color is, from 0 to 255, with lower being darker. The image is converted into HSV mode using `cv2.cvtColor`. ([More information here](https://docs.opencv.org/4.x/df/d9d/tutorial_py_colorspaces.html))

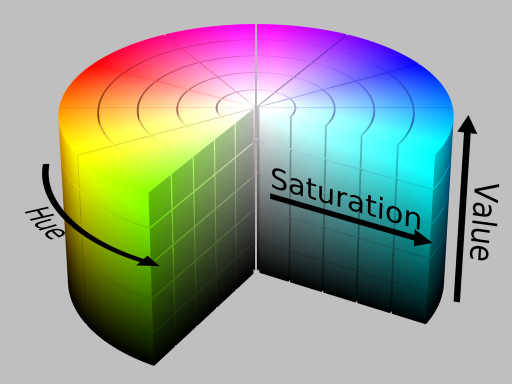
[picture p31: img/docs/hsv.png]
HSV Image


Using `cv2.inRange`, a mask for red colors and green colors is created to filter out the traffic lights. For red pillars, two calls of `cv2.inRange` is necessary because the hue value has 180 to be red as well as 0. The two masks created for red are merged with `cv2.bitwise_or`. The masks are then blurred to remove noise using `cv2.medianBlur`.

Using `cv2.cvtColor`, the image is turned into grayscale, and blurred using `cv2.GaussianBlur`. Then, using `cv2.Canny`, edges are detected in the image.

Results:
| | | |
| --- | --- | --- |
| | Undistorted image from previouscooked IMAGE | |
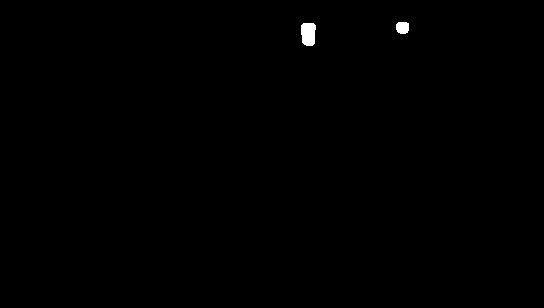
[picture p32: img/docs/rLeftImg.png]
red filtered
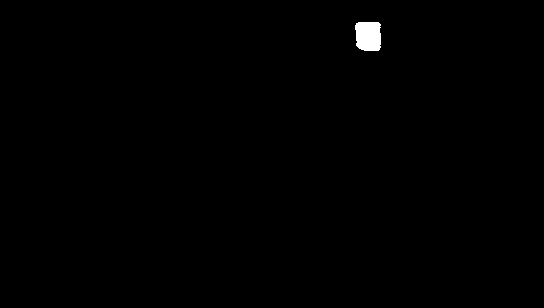
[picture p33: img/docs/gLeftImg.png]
green filtered
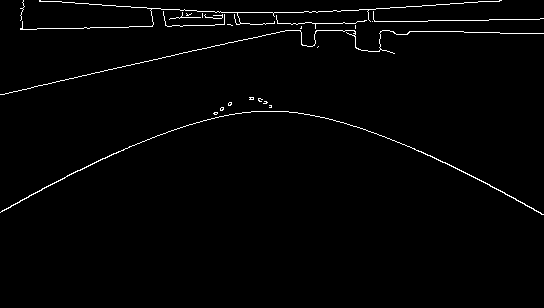
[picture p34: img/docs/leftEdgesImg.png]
edges
| Red pillar mask | Green pillar mask | Wall edge mask |
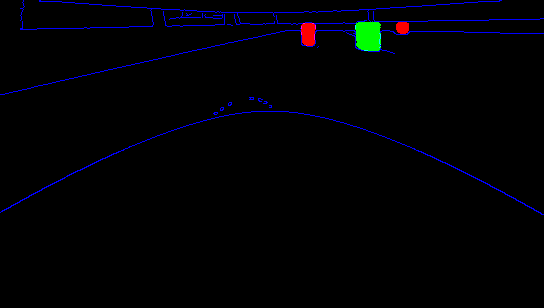
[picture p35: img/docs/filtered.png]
combined
| | Combined output to control panel | |

***

### Finding Contours

Right now, we only have two images containing only red pixels and only green pixels. The purpose of this step is to find a bounding box of the red/green pixels to represent the pillars. This bounding box has a center (x,y) coordinate, width, and height. With this information, we can calculate the distance to the top point of the pillar. The algorithm to do this will be explained in [Merge Contours & Wall Lines](#merge-contours--wall-lines).

Using `cv2.Canny`, edges can be found on the masked red or green image. To make sure `cv2.Canny` functions, a border is added using `cv2.copyMakeBorder`. The edges are blurred using `cv2.medianBlur`. Now, `cv2.findContours` can be used to find the contours on the image of edges. After finding the contours, using `cv2.contourArea` and `cv2.moments`, we can get the area and position of the contour. If the contour is smaller than `minContourSize`, or if the contour is above the walls, it gets thrown out.

***

### Finding Wall Heights

We find the "height" of the walls, which is the distance between the top edge and bottom edge. Similarly to the pillars, this information is used later to find the distance from the car to any point on the top boundary of the wall.

The edge image is cropped to remove areas on the top and bottom of the image. The left camera is slightly tilted, so some areas of the left image get set to 0. `numpy.argmax` will find the index of the largest element in each subarray of the image. However, because the image only contains values of 0 and 255, `numpy.argmax` will return the first largest value, which is at the edge of the wall. If no 255 values are found, `numpy.argmax` returns 0, which is a problem. To fix this, an array filled with a value of 255 is stacked to the end of the image using `numpy.hstack`.

***

### Finding Wall Lines

This step turns the wall heights into some lines. Each line represents a straight wall.

To find wall lines, we create a new image with only the bottom of the wall. For every pillar, the nearby wall heights get set to 0 based on the size of the contour. Creating this image is optimized using `numpy.zeros`. The bottom of the wall is set to 255. We first create a list of indices so we can quickly set all the values to 255.

Using `cv2.HoughLinesP`, we can find lines on this newly created image. After sorting the lines based on the x value, similar slope lines are merged.

Results:

The wall lines are the pink lines on the image. The white shaded areas are the wall heights.

| Left camera | Right camera |
| --- | --- |
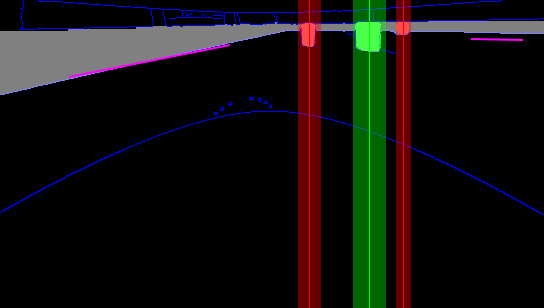
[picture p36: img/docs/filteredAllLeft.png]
Left Contours and Wall Lines
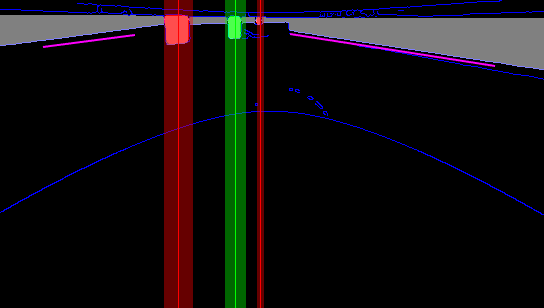
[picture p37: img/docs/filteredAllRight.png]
Right Contours and Wall Lines
|  |  |

*Note: The wall lines in the SPARK Control panel do not perfectly align with the actual locations of the lines due to offsets added to the wall search code. They are still representative of the walls, though.*

***

### Merge Contours & Wall Lines

We can find the distance to any point on the top of the wall. Diagram 1 is a side view of the camera and the wall. Our cameras are positioned at the same height as the wall, so the top of the wall forms a straight line on the image. In diagram 1, the right line is the wall, which we know is 10cm tall. $d$ is the distance we want to calculate. $newf$ is the new focal length, which we will calculate later. $h$ is the height of the wall in pixels, which we get when we find the wall heights. The two triangles are similar, so $\frac{new f}{h} = \frac{d}{10cm}$. Isolating $d$ gives us $d = \frac{10cm \times newf}{h}$.

To calculate $new f$, we need to know the base focal length. For our undistorted image, we use an approximation of 110px as the base focal length. Diagram 2 is a birds-eye view of the camera. $f$ is the base focal length, and $x$ is the x position of the wall relative to the center. Using the Pythagorean theorem, we get $new f = \sqrt{f^2 + x^2}$.

<div align=center>

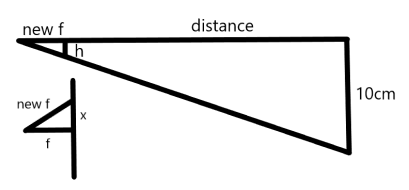
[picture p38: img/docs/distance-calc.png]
focal length


</div>

Using this algorithm, which is in `getRawDistance`, we can convert the contours into x and y positions relative to the vehicle. For wall lines, we convert each endpoint and connect them together.

**The contours and wall lines are merged from the left and right camera. This is why you see duplicate pillars.**

Results:

| Mapped Contours and Wall Lines                       |
| ---------------------------------------------------- |
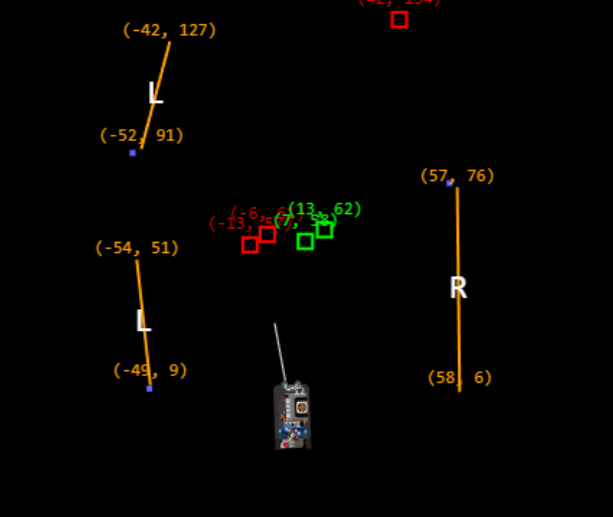
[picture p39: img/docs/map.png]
Mapped Contours and Wall Lines
|  |

***

### Transforming Walls and Pillars

It is important to know which wall is the center wall, the left wall, and the right wall. When the car is straight, the center wall is the wall in front of the car. In the image, the center wall is a horizontal line.

When the car is at an angle, the walls relative to the car will not be perfectly horizontal or perfectly vertical.

| Wall Classification | Angled Walls |
| --- | --- |
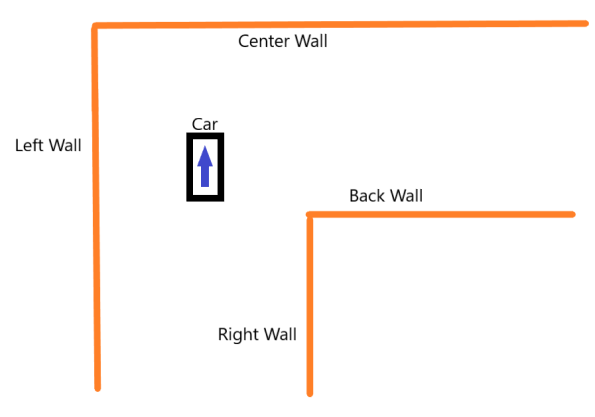
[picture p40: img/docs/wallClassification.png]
Wall Classification
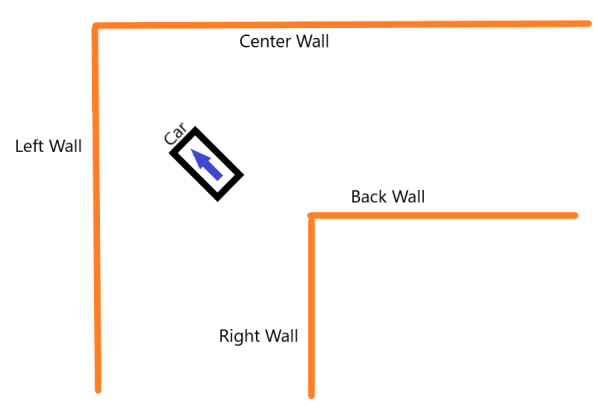
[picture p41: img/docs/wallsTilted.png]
Angled Walls
|  |  |

In this image to the right, the car sees the center wall at an angle of 45 degrees and the left wall at an angle of 45 degrees. Now, the car doesn't know which wall is the center wall.

To solve this problem, we store the orientation of the car (relative to the mat). Before processing the walls, we rotate them based on the last orientation. This makes it easy to categorize the walls. Updating the orientation is discussed below.

***

### Categorizing Walls

At this step, the wall lines have been turned into line segments that represent the real positions of the walls on the mat.

We have 5 possible categories of Walls: Left, Center, Right, Back, and Unknown. If the wall is perpendicular relative to the driving direction, it is categorized as a center or back wall depending on if it is in front or the back of the car. If the wall is parallel to the driving direction, it is categorized as a left wall or right wall depending on if it is to the left or the right of the car.

Now, depending on how slanted the wall is, we can calculate our car orientation. For example, if the center wall is tilted 5 degrees to the right, we know our car is also tilted 5 degrees to the left in addition to the current orientation.

The car orientation is thus updated.

***

### Filtering Traffic Signals

We find the largest pillar. If there are multiple pillars around the same spot we take the average of their positions.

***

# Steering and Motion Planning

All code for the Steering and Motion Planning is in `/Program/Controller/controller.py`.

***

### Finding Lap Direction

At the start of the program, we need to know if we are going clockwise or counterclockwise. This is done by searching for a jump in the wall. If a jump is detected, it means there is a gap there, allowing us to find the direction.

| Jump in Wall Height                         
| --------------------------------------------
| Jump in Wall Height |

For the first 9 frames, we search for a jump in the wall. Using `numpy.diff`, we can find differences in the wall heights. After this, we split the two images from both cameras into 4 images. The left camera image gets split at 3/4 and the right camera gets split at 1/4. The left parts are used to detect a gap on the left, while the right parts are used to detect a gap on the right. Now, we use `numpy.argmax` to find the first large difference on all 4 images. We add the difference of the indices for the left and the indices for the right to `carDirectionGuess`. If `carDirectionGuess` is greater than 0, then we are going clockwise, otherwise, we are going counterclockwise.

***

### Calculating Steering

We calculate the average distance to the left walls, center walls, and right walls.

# Open Challenge

We run the same code, except without any pillar cases.

# Obstacle Challenge
We have 4 states the car can be in.
- U-turning
- In Center Section
- Steering for pillars
- Default case

1. **U-Turning**

    The car uses the pillar it sees before the uTUrn starts to know which direction to turn. This pillar is stored in `slam.uTurnAroundPillar`. If it is red, we turn counterclockwise around it. If it is green, we turn clockwise around it. Our steering value is 100 if we are turning clockwise, and -100 if we are turning counterclockwise.

    We use the gyro to estimate that we have turned 180 degrees. When the gyro says the UTurn is done, it goes back to the other states.

2. **In Center Section**

    In this section, we have to turn based on the pillar in the next section.

    If there is no pillar, we turn when the center wall is close enough.

    If there is a red pillar and we are turning clockwise or there is a green pillar and we are turning counterclockwise, we will turn earlier than the pillar to pass on the correct side.

    If there is a green pillar and we are turning clockwise or there is a red pillar and we are turning counterclockwise, we will turn later to pass behind the pillar.

    | Red Pillar Turning                        |Green Pillar Turning
    | --------------------------------------------| --
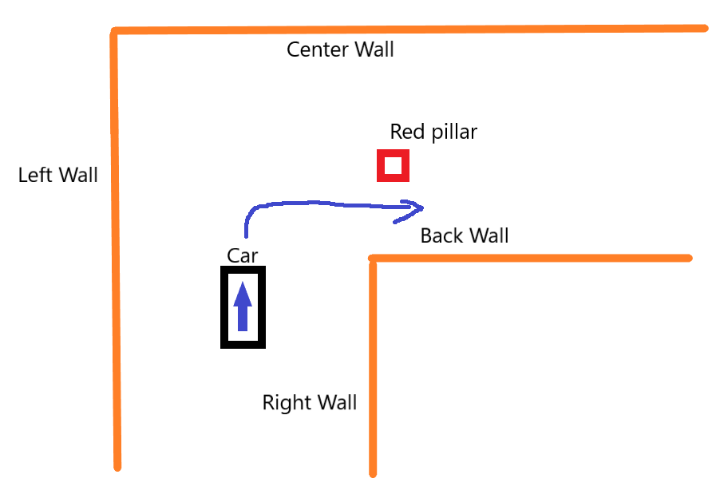
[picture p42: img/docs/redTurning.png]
Red Pillar Turning
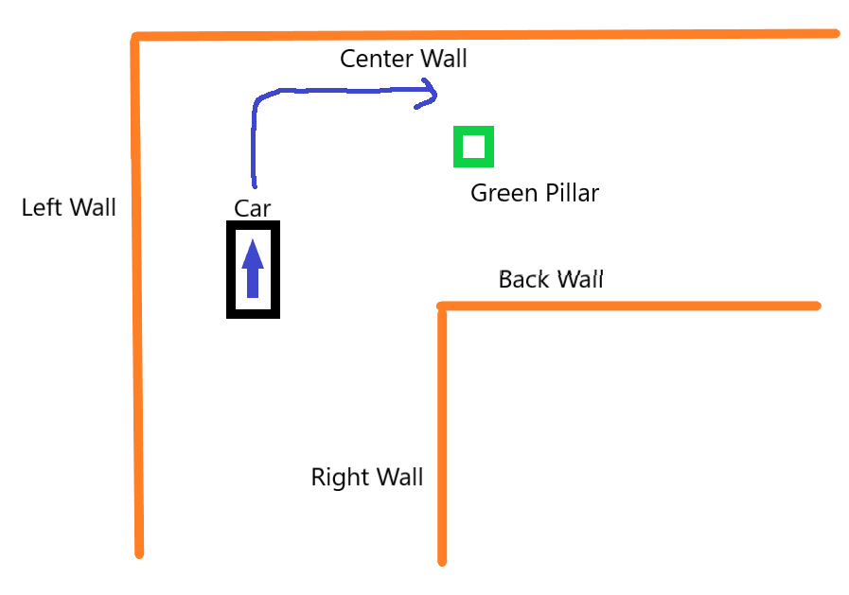
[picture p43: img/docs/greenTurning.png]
Green Pillar Turning
    |  | |

3. **Steering for Pillars**

    The car will calculate a waypoint 10cm behind the pillar and 15cm to the left or right of the pillar and steer towards this waypoint. If we are already to the right of a red pillar or the left of a green pillar, the car will instead use the default case.

4. **Default Case**

    The car will check if the left wall or right wall is too close. If it is, it will steer away from the wall. If it is not, the car will try to keep its orientation aligned with the driving direction.

***

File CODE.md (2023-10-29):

<div align=center>

banner

</div>

# Contents
* [Algorithm](#algorithm)
    * [Outline](#general-outline)
    * [Image Processing](#image-processing)
    * [Simple Driver](#simple-driver)
* [Code Structure](#code-structure)

***

# Algorithm

One  and motion planning. Our code processes the camera image and uses it to find the position of the walls relative to the car and the position of the pillars. Using this information, we can figure out where we are supposed to go next and steer accordingly.

The main consideration for our algorithm is to balance localization accuracy and speed. For localization accuracy, our target is to know which section we are in, and how far away the walls and pillars are. We need to know which section we are in to count how many laps we has completed, and to know when to uturn. We need to know how far away the car is from walls and pillars for collision avoidance.

For motion planning, our controller finds a waypoint based on the pillar position and wall position, and the car will steer towards the waypoint. The waypoint will be updated every iteration. For the uturn, the car will turn around the first pillar in the section.

Our program runs a constant update loop. All controller code can be found in `./Program/Controller/`, and is divided into three main modules: The `converter`, which pre-process images; `slam`, which is a modified SLAM (Simultaneous Localization and Mapping) algorithm with limited landmark locations; and `controller`, divided into `slamcontroller`, `simplecontroller`, and `borkencontroller` (`borkencontroller` has not been tested and `slamcontroller` is currently also borked).

## General Outline
* [Image Processing](#image-processing)
    1. Capture
    2. [Undistort](#undistorting)
    3. [Filter](#filtering)
    4. [Find wall heights](#finding-wall-heights)
    5. [Find contours](#finding-contours)
    6. [Find wall lines](#finding-wall-lines)
    7. [Merge & Convert wall lines and contours](#merge-contours--wall-lines)
* [Simple Driver](#simple-driver)
    1. [Find Car Direction](#finding-car-direction)
    2. [Categorize Walls](#categorizing-walls)
    1. [Find Car Orientation](#finding-car-orientation)
    3. [Filter Traffic Signals/Obstacles/Pillars/Game Objects](#filtering-traffic-signals)
    4. [Calculate Steering](#calculating-steering)
* SLAM Driver
    1. Non-functional (but if it works it'll be really cool)
    2. its borken

***

## Image Processing

All code for image processing is in `./Program/Controller/converter.py`.

### Undistorting

Our cameras output a distorted image, so before we can process the image, we must undistort it.

At the start of the program, cv2.fisheye.initUndistortRectifyMap is used with precalculated distortion matrices to create the remaps. See [SETUP.md](./SETUP.md#) for instructions on how to get the distortion matrix.

The undistort function calls `cv2.remap` to use the precalculated remaps to undistort the image. A new K matrix is used to partially zoom out the image to prevent too much of the image from being cropped out.

To speed up the undistorting, the top of the image is cropped before undistortion.

*All the results are of the left camera. The same calculations are done on the right camera, it is just not shown.*

| Raw Image | Undistorted Image |
| --- | --- |
| raw IMAGE | cooked IMAGE |

Because undistorting the image stretches out the edges, there are black gaps in the image on the top and bottom.

### Filtering

We filter the images to isolate the red pillars and green pillars. We also extract the edges of the walls in this step.

Using `cv2.inRange`, a mask for red colors and green colors is created to filter out the traffic lights. For red pillars, two calls of `cv2.inRange` is necessary because the hue value has 180 to be red as well as 0. The two masks created for red are merged together with `cv2.bitwise_or`. The masks are then blurred to remove noise using `cv2.medianBlur`.

Using `cv2.cvtColor`, the image is turned into grayscale, and blurred using `cv2.GaussianBlur`. Then, using `cv2.Canny`, edges are detected in the image.

Results:
| | | |
| --- | --- | --- |
| | Undistorted image from previouscooked IMAGE | |
| Red pillar maskred filtered | Green pillar maskgreen filtered | Wall edge maskedges |
| | Combined output to control panelcombined | |

### Finding Wall Heights

We find the "height" of the walls, which is the distance between the top edge and bottom edge. This is useful because we can find the distance to any point on the wall if we know the height. The algorithm to do this will be explained in [Merge Contours & Wall Lines](#merge-contours--wall-lines).

The edges image is cropped to remove areas on the top and bottom of the image. The left camera is slightly tilted, so some areas of the left image get set to 0. `numpy.argmax` will find the index of the largest element in each subarray of the image. However, because the image only contains values of 0 and 255, `numpy.argmax` will return the first value which is 255. If no 255 values are found, `numpy.argmax` returns 0, which is a problem. To fix this, an array filled with a value of 255 is stacked to the end of the image using `numpy.hstack`.

### Finding Contours

Right now, we only have two images containing only red pixels and only green pixels. The purpose of this step is to extract the pillars as an x coordinate, image width, and height. Similarly to the walls, we will be able to calculate the distance from the pillar with this information. The image width is used to remove this portion of the wall heights, as we know it is a pillar and not the wall.

Using `cv2.Canny`, edges can be found on the masked red or green image. To make sure `cv2.Canny` functions, a border is added using `cv2.copyMakeBorder`. The edges are blurred using `cv2.medianBlur`. Now, `cv2.findContours` can be used to find the contours on the image of edges. After finding the contours, using `cv2.contourArea` and `cv2.moments`, we can get the area and position of the contour. If the contour is smaller than `minContourSize`, or if the contour is above the walls, it gets thrown out.

### Finding Wall Lines

This step turns the wall heights into some lines. Each line represents a straight wall. This allows us to seperate the left wall, center wall, and right wall from each other.

To find wall lines, we create a new image with only the bottom of the wall. For every obstacle, the nearby wall heights get set to 0 based on the size of the contour. Creating this image is optimized using `numpy.zeros`. The bottom of the wall is set to 255. We first create a list of indices so we can quickly set all the values to 255.

Using `cv2.HoughLinesP`, we can find lines on this newly created image. After sorting the lines based on the x value, similar slope lines are merged.

Results:

| Left camera | Right camera |
| --- | --- |
| Left Contours and Wall Lines | Right Contours and Wall Lines |

### Merge Contours & Wall Lines

We can find the distance to any point on the top of the wall. Diagram 1 is a side view of the camera and the wall. Our cameras are positioned at the same height as the wall, so the top of the wall forms a straight line on the image. In diagram 1, the right line is the wall, which we know is 10cm tall. $d$ is the distance we want to calculate. $newf$ is the new focal length, which we will calculate later. $h$ is the height of the wall in pixels, which we get when we find the wall heights. The two triangles are similar, so $\frac{new f}{h} = \frac{d}{10cm}$. Isolating $d$ gives us $d = \frac{10cm \times newf}{h}$.

To calculate $new f$, we need to know the base focal length. For our undistorted image, we use an approximation of 80px as the base focal length. Diagram 2 is a birds-eye view of the camera. $f$ is the base focal length, and $x$ is the x position of the wall relative to the center. Using the Pythagorean theorem, we get $new f = \sqrt{f^2 + x^2}$.

<div align=center>

focal length

</div>

Using this algorithm, which is in `getRawDistance`, we can convert the contours into x and y positions relative to the vehicle. For wall lines, we convert each endpoint and connect them together.

*The contours and wall lines are merged from the left and right camera. This is why you see duplicate pillars.*

Results:

| Mapped Contours and Wall Lines                       |
| ---------------------------------------------------- |
| Mapped Contours and Wall Lines |

***

## Simple Driver

All code for the simple driver is in `./Program/Controller/simplecontroller.py`.

### Finding Car Direction

At the start of the program, we need to know if we are going clockwise or counterclockwise. This is done by searching for a jump in the wall. If a jump is detected, it means there is a gap there, allowing us to find the direction.

For the first 9 frames, we search for a jump in the wall. Using `numpy.diff`, we can find differences in the wall heights. After this, we split the two images from both cameras into 4 images. The left camera image gets split at 3/4 and the right camera gets split at 1/4. The left parts are used to detect a gap on the left, while the right parts are used to detect a gap on the right. Now, we use `numpy.argmax` to find the first large difference on all 4 images. We add the difference of the indices for the left and the indices for the right to `carDirectionGuess`. If `carDirectionGuess` is greater than 0, then we are going clockwise, otherwise we are going counterclockwise.

### Transforming Walls and Pillars

It is important to know which wall is the center wall, the left wall, and the right wall.

| Wall Classification                       |
| ---------------------------------------------------- |
| Wall Classification |

When the car is tilted, the walls relative to the car will not be straight.

| Tilted Walls                       |
| ---------------------------------------------------- |
| Tilted Walls |

In this image, the car sees the center wall tilted by 45 degrees and the left wall also tilted by 45 degrees. Now, the car doesn't know which wall is the center wall.

To solve this problem, we store the orientation of the car. Before processing the walls, we rotate it based on the last orientation. This makes it easy to categorize the walls. Updating the orientation is discussed below.

### Categorizing Walls

<!-- UPDATE!!! -->
buh we need the orientation stuff

We have 5 possible categories of Walls: Left, Center, Right, Back, and Unknown. If the wall is horizontal relative to the car, it is categorized as a center or back wall depending on if it is in front or in the back. If the wall is vertical, it is categorized as a left wall or right wall depending on if it is to the left or to the right.

Now, depending on how slanted the wall is, we can calculate our car direction. For example, if the center wall is tilted 5 degrees to the right, we know our car is also tilted 5 degrees.

### Filtering Traffic Signals

We find the largest pillar. If there are multiple pillars around the same spot we take the average of their positions.

### Calculating Steering

We calculate the average distance to the left walls, center walls, and right walls. Based on the relative angles of the walls, we can calculate the angle of the car relative to the map. There are 3 cases for steering:

1. Center wall < 110cm
2. We are Uturning
3. Default case

In case 1, if there is no pillar detected, the Car will keep straight and turn when the center wall is less than 70cm away. If there is a pillar detected, the Car will turn when the pillar is close enough to pass in front or behind it.

<!-- NOT 3 POINT TURN ANYMORE!!! -->

In case 2, NOTHING BECAUSE ITS NOT 3 POINT TURN OOF uses a precalculated set of instructions for making the 3 point turn. The gyro is used to determine how far we have turned.

In case 3, if there is no pillar detected, the Car will keep straight. If there is a pillar, it will calculate a tangent to the circle of radius 20cm centered on the pillar. The car calculates the left tangent for green pillars and the right tangent for red pillars. Then, it tries to keep itself pointed towards that tangent point.

***

# Code Structure

Converter.py has all the code for image processing. Converter.py
simplecontroller.py has all the code for the driver.
<!-- talk about how the code is segmented, what modules are made to handle what tasks (not too much detail though) -->

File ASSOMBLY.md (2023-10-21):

<div align=center>

banner

</div>

***

# Build Guide

This is the build guide for SPARK's 2023 WRO Future Engineers solution - SPARK G2. It is segmented into ***TBD*** main steps, with more detailed steps within. It assumes you have necessary tools and miscellaneous materials including but not limited to: M2.5, M3 driver bits; a Dupont connector crimpange kit; a 3D printer; a soldering iron; 20-24 gauge wire; and M2.5, M3 flat/countersunk screws.

Below is a more-or-less detailed step-by-step guide to recreate SPARK g2.

***

# Contents

* [Parts List](#parts-list)
* [Chassis Assembly](#chassis-assembly)
* [Jetson Nano Setup](#jetson-nano-setup)
    * [Board Setup, SSHFS, Static IP](#board-setup-sshfs--static-ip)
    * [Enable GPIO & I2C](#enable-gpio-and-i2c)
    * [Install Packages](#package-installation)
    * [Remove GUI, Autologin, & Run-on-startup](#text-only-auto-login--run-on-startup)
    * [SPARK Control Panel Setup](#setup-for-spark-control-panel)
    * [Camera Calibration](#camera-calibration)

***

## Parts List

* Parts from [Schumacher Atom 2 S2 1/12 GT12 Competition Pan Car Kit](https://www.amainhobbies.com/schumacher-atom-2-s2-1-12-gt12-competition-pan-car-kit-schk179/p1055346) (not sponsored)
    * [Drive Pod Parts](https://www.racing-cars.com/gt12/atom-2/atom-2-parts=chassis-parts/s2-pod-parts-atom-2-u7905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)
    * [Assembled Differential](https://www.racing-cars.com/gt12/atom-2/atom-2-parts=transmission/assembled-diff-atom-2-u7713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)
    * [Left Drive Wheel Clamp](https://www.racing-cars.com/gt12/atom-2/atom-2-parts=transmission/lh-drive-clamp-a1-a2-u4853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)
    * Transmission Housings: [Left Side](https://www.racing-cars.com/gt12/atom-2/atom-2-parts=transmission/trans-housing-lh-a2-3-e2-e5-u7483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), [Right Side](https://www.racing-cars.com/gt12/atom-2/atom-2-parts=transmission/trans-housing-rh-a2-3-e2-e3-e4-u7484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)
    * [Ride Height Adjusters](https://www.racing-cars.com/gt12/atom-2/atom-2-parts=suspension/ride-height-adjusters-0-25-1-75-4prs-e1-5-ic-2-a3-u4973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) (use 1.75mm)
    * 2x [LP Front Axle](https://www.racing-cars.com/gt12/atom-2/atom-2-parts=suspension/low-profile-front-axle-a1-a3-u7302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)
    * [Rear Axle Ball Bearings](https://www.racing-cars.com/gt12/atom-2/ball-bearing-1-4x3-8x1-8-flanged-yellow-pr-u4980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)
    * [Front Axle Ball Bearings](https://www.racing-cars.com/gt12/atom-2/ball-bearing-1-8x5-16-flanged-yellow-pr-u4981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)
    * [Steel shims](https://www.racing-cars.com/gt12/atom-2/s-steel-shims-1-4x5-16x0-004-ss-at-ecl-u4112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)
    * [M3 Nyloc Nuts](https://www.racing-cars.com/gt12/atom-2/m3-alloy-nyloc-nuts-low-profile-black-pk10-cr517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)
    * [Servo Horn](https://www.racing-cars.com/gt12/atom-2/atom-2-parts=chassis-parts/25t-servo-saver-assembly-a2-e3-e4-u7895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)
    * [Ball Studs (short)](https://www.racing-cars.com/gt12/atom-2/pro-ball-stud-short-pk4-u4274?returnurl=%2fgt12%2fatom-2%2f)
* [Yahboom Jetson Nano 4GB Developer Kit](https://category.yahboom.net/collections/jetson/products/jetson-nano-sub)
* 2x [Arducam Raspberry Pi Official Camera Module V2, with 8 Megapixel IMX219 Wide Angle 175 Degree Replacement](https://www.amazon.com/Arducam-Raspberry-Official-Megapixel-Replacement/dp/B083PW4BLH/)
* [Intel AX201 WiFi 6 BT 5.1 M.2 2230 with 10in RP-SMA Antenna](https://www.newegg.com/p/0XM-009Y-001C7) (not required but helpful)
* [Noctua NF-A4x10 5V](https://noctua.at/en/products/fan/nf-a4x10-5v) (not required)
* [HobbyWing QUICRUN 10BL60 Brushless ESC Sensored](https://www.hobbywingdirect.com/products/quicrun-10-sensored)
* [HobbyWing QUICRUN 3650 Sensored Brushless Motor G2 (25.5T)](https://www.hobbywingdirect.com/collections/quicrun-brushless-motor-series-sensorless/products/quicrun-3650-sensored-2-pole-brushless-motor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)
* [Savox SV1261MG Digital Mini Servo](https://www.savoxusa.com/products/sv1261mg-mini-digital-high-voltage-aluminum-case-servo-0-095-277-7-4v)
* A LiPo balance charger with XT-60 connector, rated for 3S
* [Zeee Premium Series 3S LiPo Battery 4200mAh 11.4V 120C with XT60 Plug](https://www.amazon.com/Zeee-Premium-Compatible-Helicopter-Airplane/dp/B09CMLSK67)
* 2x [DC-DC 5A Adjustable Buck Converter](https://www.amazon.com/Adjustable-Converter-1-25-36v-Efficiency-Regulator/dp/B079N9BFZC)
* [DC Digital Voltometer](https://www.amazon.com/bayite-Digital-Voltmeter-Display-Motorcycle/dp/B00YALUXH0/)
* [Male 5.5mm DC Barrel Connectors](https://www.amazon.com/Pigtails-Female-Connector-Pigtail-Security/dp/B08PYWN3T7/)
* [Panel-Mountable Female XT60 Connectors](https://www.amazon.com/XT60E-M-Mountable-Connector-Models-Multicopter/dp/B07YJMCDC3)
* [Normally Closed/Momentary On Push Button](https://www.amazon.com/Pieces-normally-closed-Button-Momentary/dp/B07HCLVMGS/) (size must match)
* [12 Tooth 48 Pitch Pinion Gear with Set Screw](https://www.amazon.com/Traxxas-PINION-PITCH-SCREW-2428/dp/B00EFXMUO2)
* [78 Tooth Spur Gear 48 Pitch](https://www.amazon.com/Kimbrough-Pitch-Spur-Gear-78T/dp/B0006O1QVM)
* 20-24 gauge wire
* M3 nylon screws (6mm)
* M3 nylon standoffs (6mm works best)
* M3 nylon nuts
* M3 nuts
* Countersunk, cap head M3 screws (6mm and 8mm work best)
* Socket cap head M3x40mm screws [(like these)](https://www.amazon.com/Alloy-Steel-Socket-Screws-Black/dp/B00W97R5KU)
* Differential lubrication

You will need (at least) the following tools:
* 3D printer or access to 3D printing service
* Hex Allen drivers (key or bits)
* Phillips head drivers
* Rotary tool with grinding bit (depending on which version of motor)
* Crimper tool
* Soldering iron

*There may be items not listed that are used in the build guide, we apologize if that happens.*

***

## Chassis Assembly

Sorry! We couldn't get detailed step-by-step instructions in time! Print out the parts located in `/dist/3D Models/`. in their given orientation (they have been oriented for the best print results) Most of the assembly should be fairly simple (the rear axle assembly should be bought from [Schumacher Racing's site](https://www.racing-cars.com/gt12/atom-2/) and NOT PRINTED), and follow the [pinout sheet](https://docs.google.com/spreadsheets/d/1WAe1DtCbWhLoC4L6yzJYvS99iHG4yAiWakqxsy8os7s/edit?usp=sharing) and connect to their corresponding pins on the other boards. Some holes may need to be drilled out and some crimping may have to be done.

If you need a reference model we have our [OnShape document linked](https://cad.onshape.com/documents/82dd14d30b814e8846567203/w/34e1b6a4058ed5fbde8ef66a/e/47aa4028e09ec17a24a63590). (The ESC and IMU have not been modeled. The ESC goes in the rear, within the raised rectangle. The IMU should be mounted to the 4 unpopulated holes with M2.5 screws.)

Follow the diagram below to wire the button and indicator LEDs.
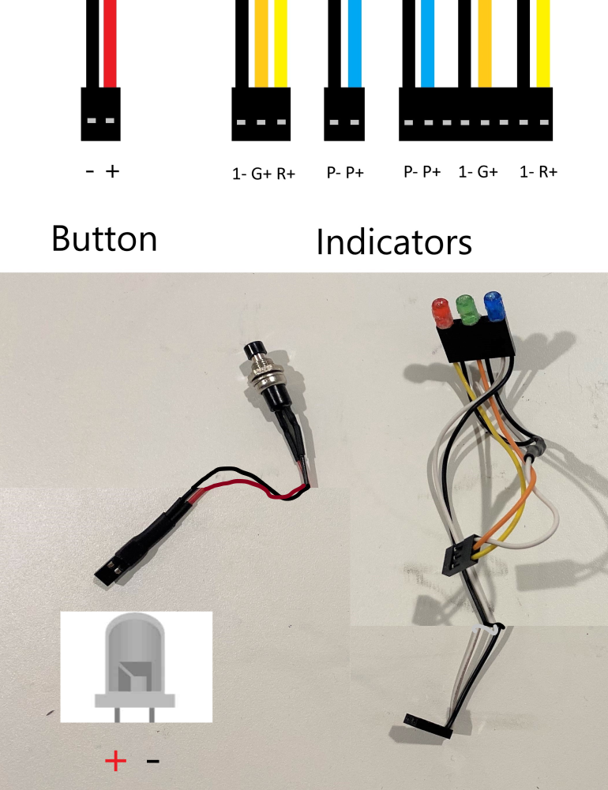
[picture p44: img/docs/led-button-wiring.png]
Button and indicator LED wiring


*Note: For I2C connectors, Yellow should be SCL and blue should be SDA; there is no set standard.*

For soldering, we recommend soldering the regulators to their own connectors **in parallel**, and using that as a pass-through to the ESC. The female connectors should be used on the ESC inputs and regulator input, and the male connector on the pass through end of the regulator wires. See the diagram below.

Wiring for regulator passthrough

Follow the quick start guide for the ESC to solder the motor connections. Brief summary: solder A, B, and C connectors to the motor (or supplied connectors). Ensure the sensor wire is secure before mounting motor and ESC.

**WARNING:** DO NOT CONNECT THE ESC 3-PIN DIRECTLY TO THE SERVO DRIVER! IT WILL BACKDRIVE THE REGULATOR AND BREAK IT! ONLY CONNECT THE PWM PIN (white)!

***

## Jetson Nano Setup

### Board Setup, SSHFS, & Static IP

Visit [Yahboom](http://www.yahboom.net/)'s [setup and tutorial repository](http://www.yahboom.net/study/jetson-nano) to begin setting up the [Jetson Nano 4GB](https://category.yahboom.net/collections/jetson/products/jetson-nano-sub). Follow steps 1.1-1.7 in "Development setup > SUB Version".

-> http://www.yahboom.net/study/jetson-nano

After setting up the board, follow step 2.1 in section "Basic Settings" to log into your Jetson Nano. Keep PuTTY open, as it will be used for the rest of the setup process. Also keep the IP. For remote file transfer, install sshfs (linux only), or use [sshfs-win](https://github.com/winfsp/sshfs-win) from WinFsp. Follow instructions to mount the Jetson Nano to a network drive. Now upload all contents of the `/Program/` folder into a new folder on the Jetson Nano. Remember the directory of the folder, this will be used later.

*This method should be used to upload programs.*

Make sure a static IP is set to the board to make SSH and file transfer easier. Go to your router settings and [assign a DHCP reservation (PCmag)](https://www.pcmag.com/how-to/how-to-set-up-a-static-ip-address) (or a straight static IP) to your Jetson Nano. Save this IP in your PuTTY settings and SSHFS mounting.

### Enable GPIO and I2C

Next, setting up the board for the application. First, enable GPIO and I2C. Create a new user group, and add your user to it (this is the user running the commands).

```
sudo groupadd -f -r gpio
sudo usermod -a -G gpio your_user_name
```

Copy `99-gpio.rules` from `/dist/` in the project folder to `/etc/udev/rules.d/` on the Jetson Nano. Then enable the rule.

```
sudo udevadm control --reload-rules && sudo udevadm trigger
```

<!-- Now enable PWM. Run the options file for jetson-GPIO.

```
sudo /opt/nvidia/jetson-io/jetson-io.py
```

Go down to "Configure 40-pin expansion header" and enter that submenu. Find `pwm0` and `pwm`, and enable them by selecting them and pressing "Enter". Now exit the tool. GPIO and PWM have been enabled. -->

You may need to enable permissions for I2C

```
sudo usermod -a -G i2c your_user_name
```

### Package Installation

Some packages will need to be installed. [Jetson-GPIO](https://github.com/NVIDIA/jetson-gpio), socket.io-client, [adafruit-servokit](https://github.com/adafruit/Adafruit_CircuitPython_ServoKit), and [adafruit-mpu6050](https://github.com/adafruit/Adafruit_MPU6050) must be installed (Jetson-GPIO may be pre-installed on some versions).

Use the following pip commands:

```
pip3 install adafruit-circuitpython-servokit
pip3 install adafruit-mpu6050
pip3 install "python-socketio[client]"
```

### Text-Only, Auto-Login, & Run on Startup

Switch the Jetson Nano to text-only mode (gui is almost useless for this application and only causes unneccesary slowness).

```
sudo systemctl set-default multi-user.target
```

Autologin must be done to avoid having to plug in a monitor and keyboard to start ssh and run programs. The following accomplishes it:

```
sudo systemctl edit getty@tty1
```

A temporary editor will appear. Place the following text in it, replacing "your_user_name" with your user name.

```
[Service]
ExecStart=
ExecStart=-/sbin/agetty -o '-p -f your_user_name' -a your_user_name --noclear %I $TERM
```

Save and close the editor with `:wqa`.

To run the program on startup, first obtain the directory of the program folder uploaded earlier. Create `spark_startup.service` in `/etc/systemd/system` and place the following in the contents, replacing "/filepath/" with the absolute directory of the folder (begins with a "/").

```
[Service]
WorkingDirectory=/filepath
ExecStart=/usr/bin/python3 -u /filepath/startup.py
User=username

[Install]
WantedBy=multi-user.target
```

Save the file and add permissions to it.

```
sudo chmod 644 /etc/systemd/system/spark_startup.service
systemctl enable /etc/systemd/system/spark_startup.service
```

If you wish to use the SPARK Control Panel, repeat the above steps to create a second startup service (`spark_server.service`). The contents should look like the below:

```
[Service]
WorkingDirectory=/filepath
ExecStart=/usr/local/bin/node /filepath/Util/server.js
User=username

[Install]
WantedBy=multi-user.target
```

Make sure to add the same permissions as `spark_startup.service`.

Reboot the Jetson Nano to test if these changes worked. No GUI should appear and you shuld be automatically logged in.

Enable run-on-startup by editing `run-on-startup.txt` in the folder. Replace the first line with `true`.

Go to `startup.py`, and change `path` to the absolute filepath of your directory (same as filepath in the previous steps)

Example:

```
path = '/home/nano/Documents/SPARK_FutureEngineers_2023/'
```

Reboot the Jetson Nano again

### Setup for SPARK Control Panel

SPARK uses a debugging server (SPARK Control Panel) for quick development and real-time monitoring. It runs on a separate Node.js process and is not needed. If you want access to the SPARK Control Panel you must install Node.js and dependencies.

```
sudo apt install nodejs
```

Navigate to `/Util/` and install dependencies.

```
npm install
```

For the authentication system to work properly (not actual authentication, just a UUID exchange to prevent people from sending bogus signals) `auth.json` must be created in `/Util/`.

```
vim auth.json
```

The contents should be a single UUID:

```
"214e7634-b7c3-4044-b297-533da8cfbe7f"
```

This UUID should also be present on client devices, along with the IP of the car (set earlier). On the client devices, create `/SPARK-Util/SPARK-Control/config.js`.

Example:

```
const ip = '192.168.1.151';
const auth_uuid = '214e7634-b7c3-4044-b297-533da8cfbe7f';
```

To open the SPARK Control Panel and other utilities, use `node SPARK-Util/static.js` or open the batch file `/SPARK-Util/static.bat`. In any web browser (only Chrome tested), navigate to `localhost:8081` to access the SPARK Control Panel.

### Camera Calibration

You may encounter pink fringing on the cameras. If that happens, take the following steps to fix it:

Copy `camera_overrides.isp` from `/dist/` in the project folder to `/var/nvidia/nvcam/settings/` on the Jetson Nano.

Give the overrides permissions with the next two:

```
sudo chmod 664 /var/nvidia/nvcam/settings/camera_overrides.isp
sudo chown root:root /var/nvidia/nvcam/settings/camera_overrides.isp
```

Next, calibrate the cameras. If you skip this step, the distortion correction may have error and the program may not function as intended.

First, you need to run manualdrive and take pictures of a chessboard. Take roughly 10 pictures. Place these pictures in `dist/calibration`, and then run the first cell of `calibrate.ipynb`. The program should print out DIM, K, and D. If there is an error, make sure all the pictures have the full size of the chessboard. Paste these values of DIM, K, and D into the second cell where it says `# Paste matrices here`. Run the second cell to ensure the distortion matrices work. Now you can paste K and D into `converter.py`, at line 25.

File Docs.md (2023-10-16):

<div align=center>

banner

</div>

# Contents
* [Algorithm](#algorithm)
    * [Outline](#general-outline)
    * [Image Processing](#image-processing)
    * [Simple Driver](#simple-driver)
* [Code Structure](#code-structure)

***

# Algorithm

Our program runs a constant update loop. All controller code can be found in `./Program/Controller/`, and is divided into three main modules: The `converter`, which pre-process images; `slam`, which is a modified SLAM (Simultaneous Localization and Mapping) algorithm with limited landmark locations; and `controller`, divided into `slamcontroller`, `simplecontroller`, and `borkencontroller` (`borkencontroller` has not been tested and `slamcontroller` is currently also borked).

## General Outline
* [Image Processing](#image-processing)
    1. Capture
    2. [Undistort](#undistorting)
    3. [Filter](#filtering)
    4. [Find wall heights](#finding-wall-heights)
    5. [Find contours](#finding-contours)
    6. [Find wall lines](#finding-wall-lines)
    7. [Merge & Convert wall lines and contours](#merge-contours--wall-lines)
* [Simple Driver](#simple-driver)
    1. [Find Car Direction](#finding-car-direction)
    2. [Categorize Walls](#categorizing-walls)
    1. [Find Car Orientation](#finding-car-direction)
    3. [Filter Traffic Signals/Obstacles/Pillars/Game Objects](#filtering-traffic-signals)
    4. [Calculate Steering](#calculating-steering)
* SLAM Driver
    1. Non-functional (but if it works it'll be really cool)
    2. its borken

***

## Image Processing

All code for image processing is in `./Program/Controller/converter.py`.

### Undistorting

At the start of the program, cv2.fisheye.initUndistortRectifyMap is used with precalculated distortion matrices to create the remaps. See [ASSEMBLY.md](./ASSEMBLY.md#) for instructions on how to get the distortion matrix.

The undistort function calls `cv2.remap` to use the precalculated remaps to undistort the image. A new K matrix is used to partially zoom out the image to prevent too much of the image being cropped out.

### Filtering

Using `cv2.inRange`, a mask for red colors and green colors are created to filter out the traffic lights. For red pillars, two calls of `cv2.inRange` is necessary because the hue value has 180 to be red as well as 0. The two masks created for red are merged together with `cv2.bitwise_or`. The masks are then blurred to remove noise using `cv2.medianBlur`.

Using `cv2.cvtColor`, the image is turned into grayscale, and blurred using `cv2.GaussianBlur`. Then, using `cv2.Canny`, edges are detected in the image.

### Finding Wall Heights

The edges image is cropped to remove areas on the top and bottom of the image. The left camera is slightly tilted, so some areas of the left image get set to 0. `numpy.argmax` will find the index of the largest element in each subarray of the image. However, because the image only contains values of 0 and 255, `numpy.argmax` will return the first value that is 255. If no 255 values are found, `numpy.argmax` returns 0, which is a problem. To fix this, an array filled with a value of 255 is stacked to the end of the image using `numpy.hstack`.

### Finding Contours

Using `cv2.Canny`, edges can be found on the masked red or green image. To make sure `cv2.Canny` functions, a border is added using `cv2.copyMakeBorder`. The edges are blurred using `cv2.medianBlur`. Now, `cv2.findContours` can be used to find the contours on the image of edges. After finding the contours, using `cv2.contourArea` and `cv2.moments`, we can get the area and position of the contour. If the contour is smaller than `minContourSize`, or if the contour is above the walls, it gets thrown out.

### Finding Wall Lines

To find wall lines, we create a new image with only the bottom of the wall. For every obstacle, the nearby wall heights get set to 0 based on the size of the contour. Creating this image is optimized using `numpy.zeros`. The bottom of the wall is set to 255. We first create a list of indices so we can quickly set all the values to 255.

Using `cv2.HoughLinesP`, we can find lines on this newly created image. After sorting the lines based on x value, similar slope lines are merged.

### Merge Contours & Wall Lines

We can find the distance to any point on the top of the wall. Diagram 1 is a side view of the camera and the wall. Our cameras are positioned at the same height as the wall, so the top of the wall forms a straight line on the image. In diagram 1, the right line is the wall, which we know is 10cm tall. $d$ is the distance we want to calculate. $newf$ is the new focal length, which we will calculate later. $h$ is the height of the wall in pixels, which we get when we find the wall heights. The two triangles are similar, so $\frac{new f}{h} = \frac{d}{10cm}$. Isolating $d$ gives us $d = \frac{10cm \times newf}{h}$.

To calculate $new f$, we need to know the base focal length. For our undistorted image, we use an approximation of 80px as the base focal length. Diagram 2 is a birds eye view of the camera. $f$ is the base focal length, and $x$ is the x position of the wall relative to the center. Using the pythagorean theorem, we get $new f = \sqrt{f^2 + x^2}$.

<div align=center>

focal length

</div>

Using this algorithm, which is in `getRawDistance`, we can convert the contours into x and y positions relative to the car. For wall lines, we convert each endpoint and connect them together.

***

## Simple Driver

All code for the simple driver is in `./Program/Controller/simplecontroller.py`.

### Finding Car Direction

For the first 9 frames, we search for a gap on the wall to find if we are going clockwise or counterclockwise. Using `numpy.diff`, we can find differences in the wall heights. After this, we split the two images from both cameras into 4 images. The left camera image gets split at 3/4 and the right camera gets split at 1/4. The left parts are used to detect a gap on the left, while the right parts are used to detect a gap on the right. Now, we use `numpy.argmax` to find the first large difference on all 4 images. We add the difference of the indices for the left and the indices for the right to `carDirectionGuess`. If `carDirectionGuess` is greater than 0, then we are going clockwise, otherwise we are going counter clockwise.

### Categorizing Walls

There are 4 possible categories of walls: Left, Center, Right, and Unknown. The slope of the wall relative to the car is calculated. If the slope is relatively small and the wall is in front of the car, the wall gets classified as a center wall. Otherwise, if the slope is small but it is behind the car, the wal gets classified as Unknown. If the wall is to the left of the car, it is a left wall, if it is to the right, it is a right wall.

### Filtering Traffic Signals

We find the largest pillar. If there are multiple pillars in the same spot we take the average of their positions.

### Calculating Steering

We calculate the average distance to the left walls, center walls, and right walls. Based on the relative angles of the walls to the car, we can calculate the angle of the car relative to the map. There are 3 cases for steering:

1. Center wall < 110cm
2. We are Uturning
3. Default case

In case 1, if there is no pillar detected, the car will keep straight and turn when the center wall is less than 70cm away. If there is a pillar detected, the car will turn when the pillar is close enough to pass in front or behind it.

In case 2, the car uses a precalculated set of instructions for making the 3 point turn. The gyro is used to determine how far we have turned.

In case 3, if there is no pillar detected, the car will keep straight. If there is a pillar, the car will calculate a tangent to the circle of radius 20cm centered on the pillar. The car calculates the left tangent for green pillars and right tangent for red pillars. Then, the car tries to keep itself pointed towards that tangent point.

***

# Code Structure

<!-- talk about how the code is segmented, what modules are made to handle what tasks (not too much detail though) -->

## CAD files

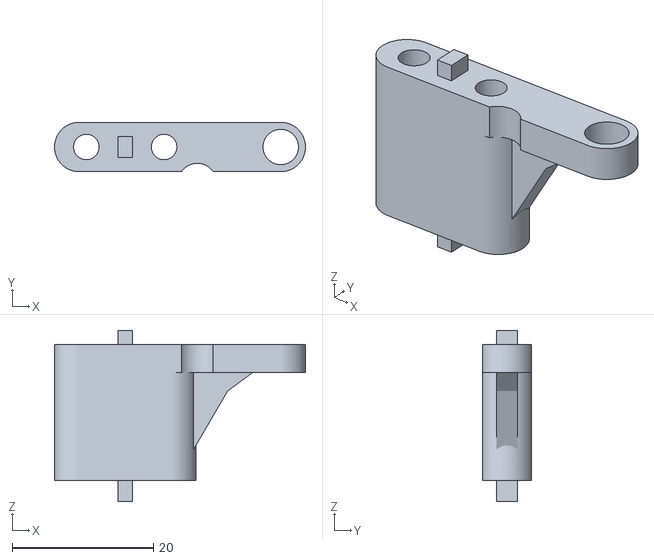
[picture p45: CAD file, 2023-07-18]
dist/3d-models/SPARK-G2-steeringtower-topleft.stl
35.5 x 7.00 x 24.2

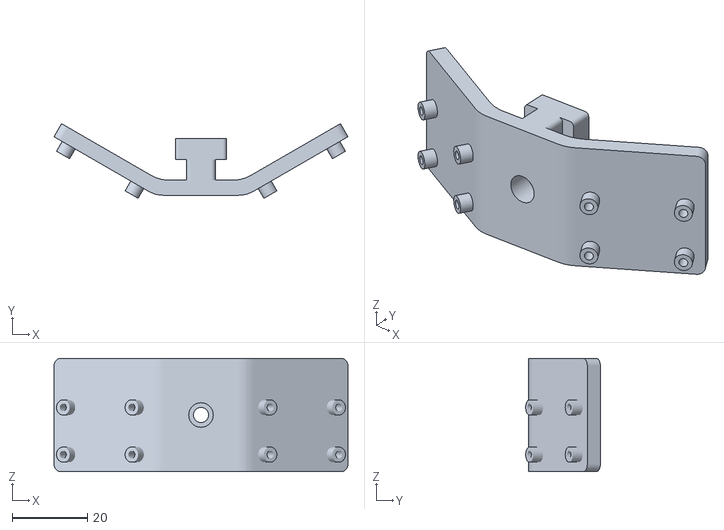
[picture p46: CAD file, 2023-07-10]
dist/3d-models/SPARK-G2-cameratower-carrier.stl
78.0 x 19.8 x 30.0

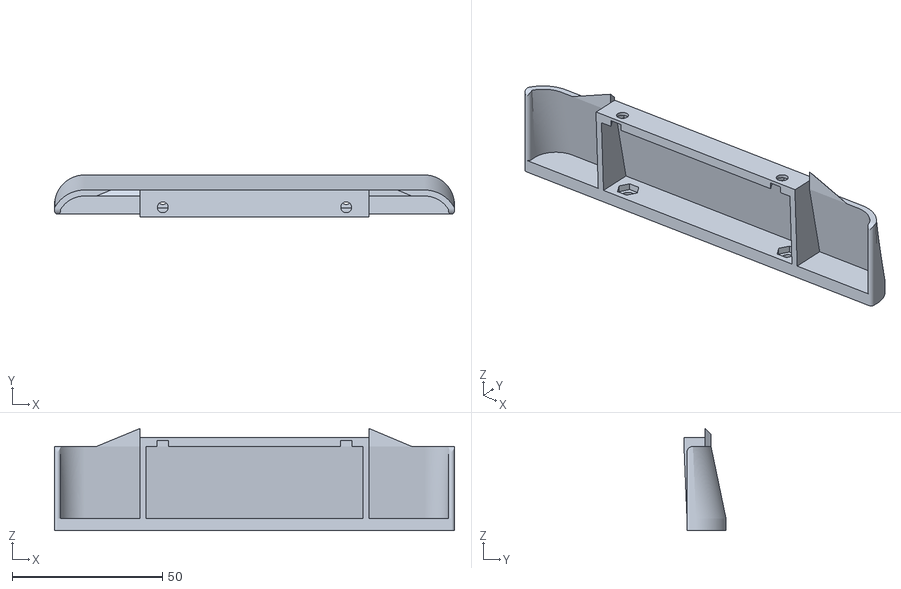
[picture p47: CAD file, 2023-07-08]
dist/3d-models/SPARK-G2-frontcover.stl
133.0 x 14.0 x 34.0

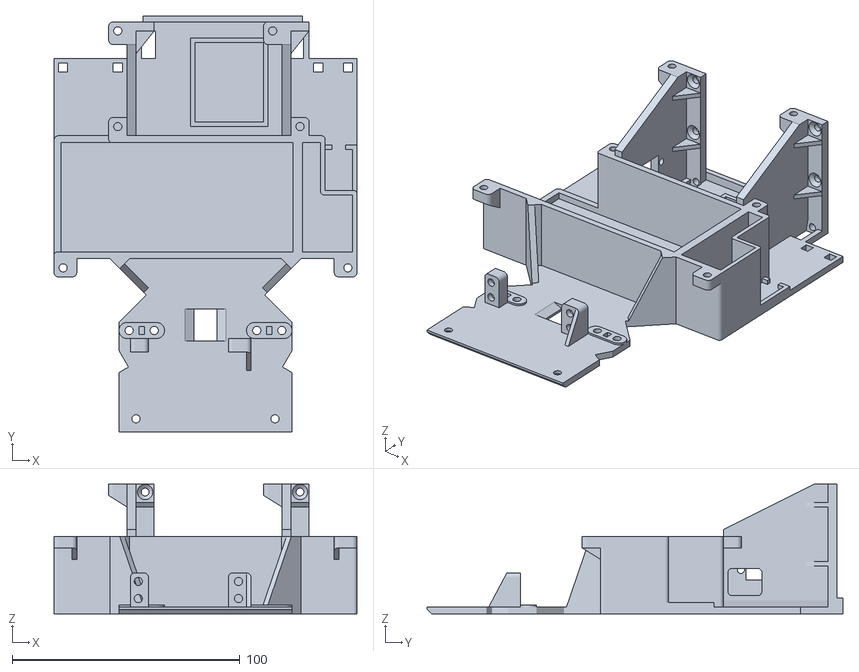
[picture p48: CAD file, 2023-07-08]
dist/3d-models/SPARK-G2-chassis-base.stl
133.0 x 182.5 x 57.0

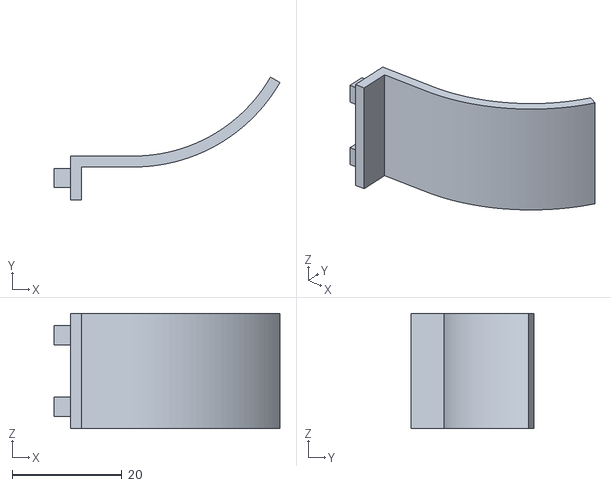
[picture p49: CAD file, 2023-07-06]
dist/3d-models/SPARK-G2-dustcover-left.stl
41.1 x 22.4 x 21.0

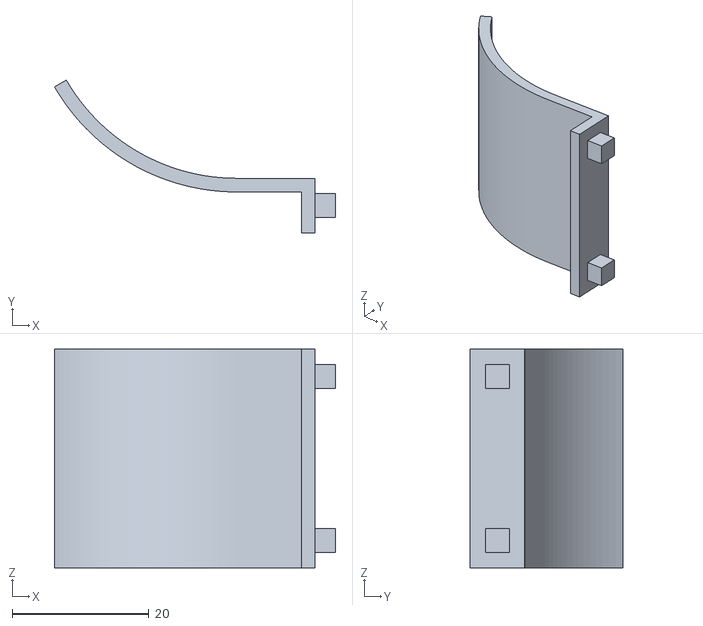
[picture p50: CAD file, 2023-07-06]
dist/3d-models/SPARK-G2-dustcover-right.stl
41.1 x 22.4 x 32.0

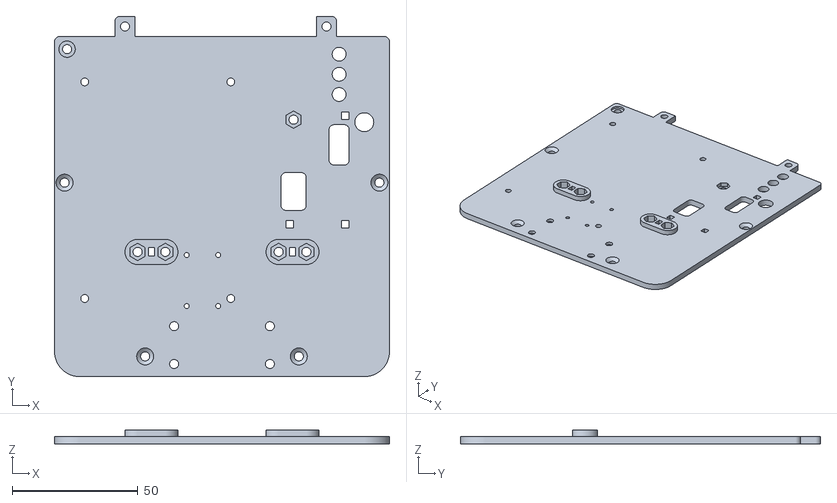
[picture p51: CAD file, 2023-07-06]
dist/3d-models/SPARK-G2-chassis-platform.stl
133.0 x 143.0 x 5.50

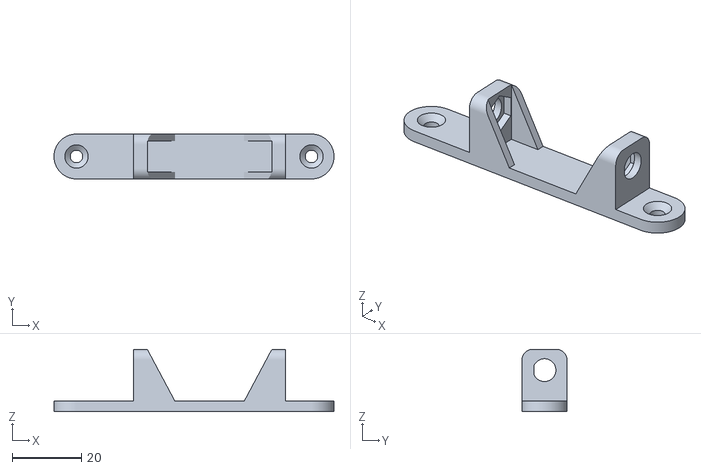
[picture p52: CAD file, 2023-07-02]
dist/3d-models/SPARK-G2-antennamount.stl
81.0 x 13.0 x 18.0

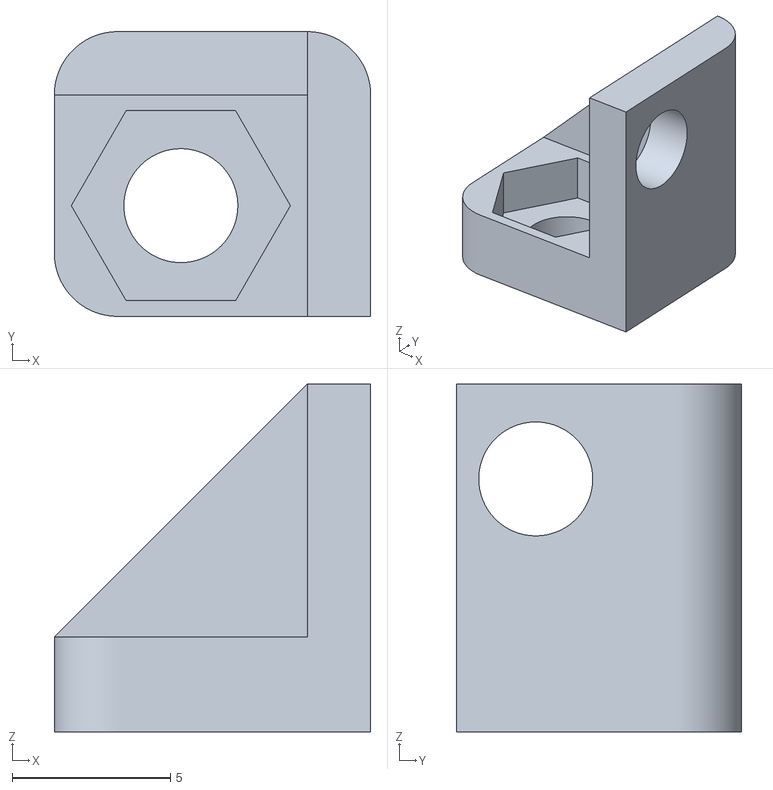
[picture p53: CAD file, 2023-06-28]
dist/3d-models/SPARK-G2-voltmeterbracket-1.stl
10.00 x 9.00 x 11.0

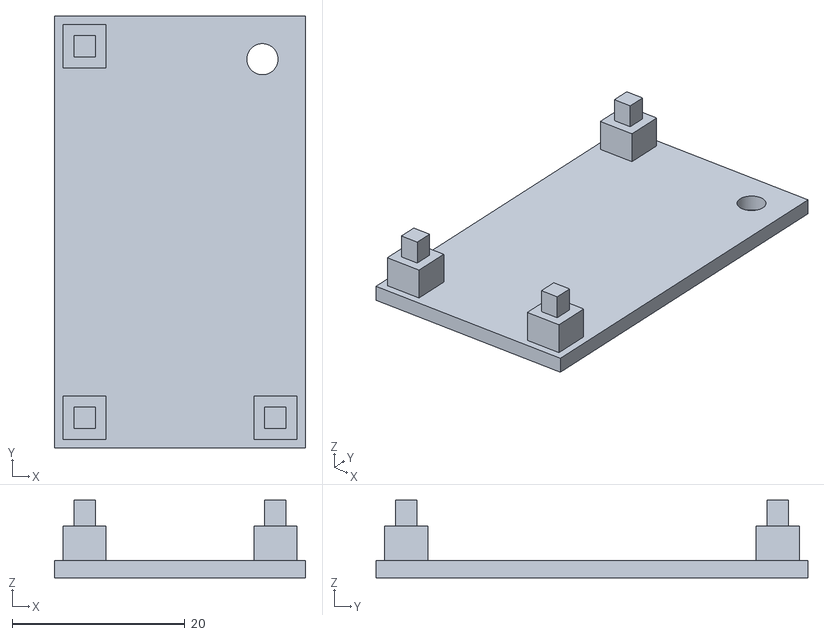
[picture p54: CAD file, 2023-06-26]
dist/3d-models/SPARK-G2-cablecover.stl
29.1 x 50.0 x 9.00

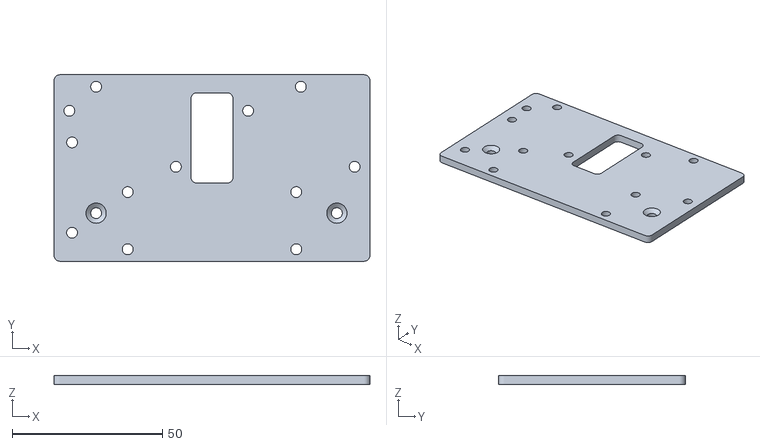
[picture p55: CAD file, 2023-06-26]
dist/3d-models/SPARK-G2-chassis-upperplatform.stl
105.0 x 62.0 x 3.00

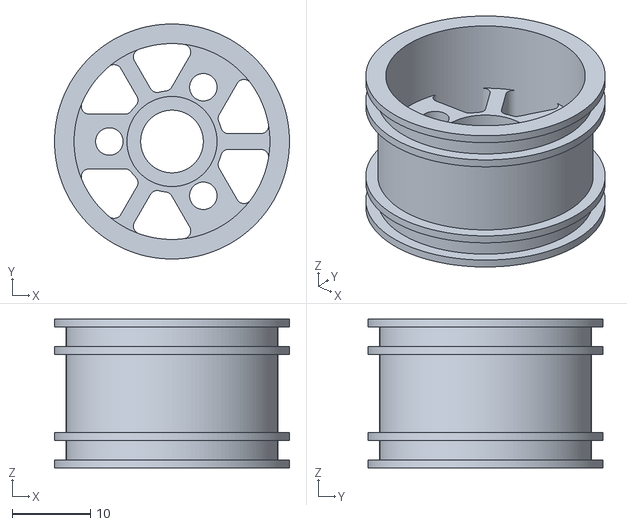
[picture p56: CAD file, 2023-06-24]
dist/3d-models/SPARK-G2-wheelrim-rear.stl
30.0 x 30.0 x 19.0

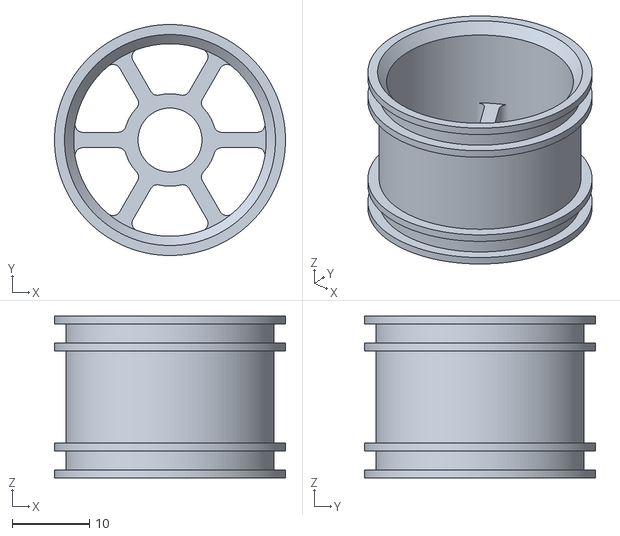
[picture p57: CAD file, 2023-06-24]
dist/3d-models/SPARK-G2-wheelrim-front.stl
30.0 x 30.0 x 21.0

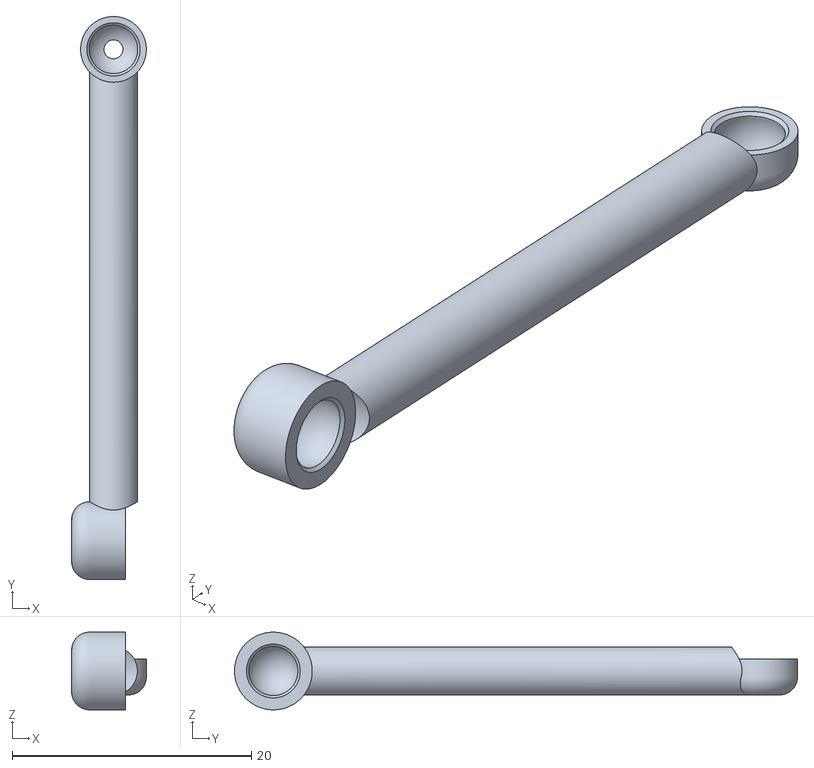
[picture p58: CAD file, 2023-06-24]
dist/3d-models/SPARK-G2-steeringtierod-right.stl
6.25 x 47.1 x 6.50

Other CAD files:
dist/3d-models/SPARK-G2-steeringtower-topright.stl
dist/3d-models/SPARK-G2-voltmeterbracket-2.stl
dist/3d-models/SPARK-G2-steeringtierod-left.stl
dist/3d-models/SPARK-G2-cameratower-rail.stl
dist/3d-models/SPARK-G2-steeringknuckle-left.stl
dist/3d-models/SPARK-G2-steeringknuckle-right.stl
dist/3d-models/SPARK-G2-steeringtower-bottom.stl

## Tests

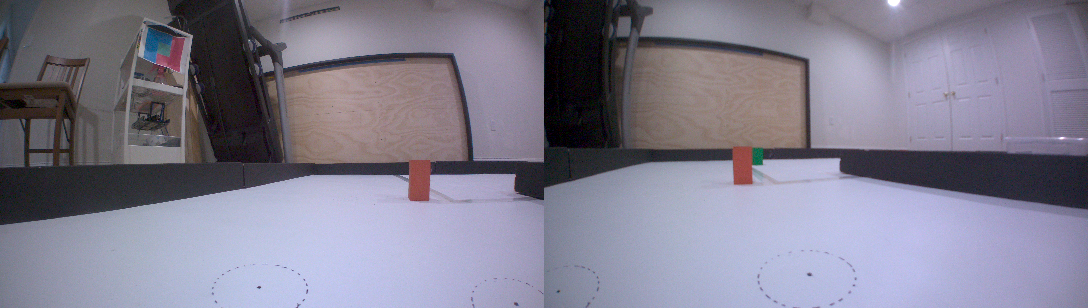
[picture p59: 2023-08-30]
dist/calibration/images/test1.png

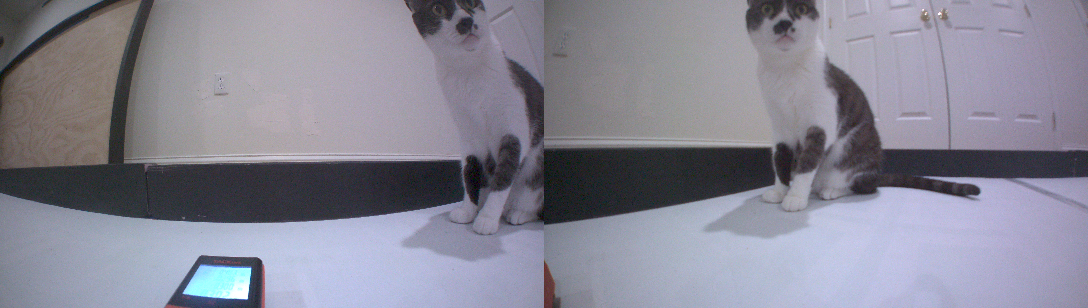
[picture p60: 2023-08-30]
dist/calibration/images/test4.png

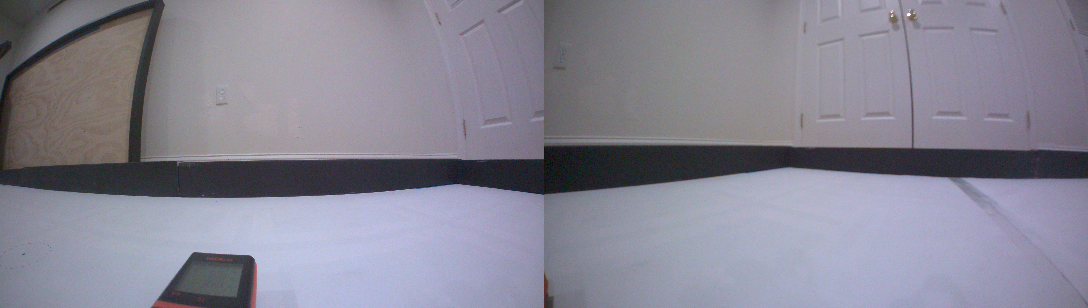
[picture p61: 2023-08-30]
dist/calibration/images/test2.png

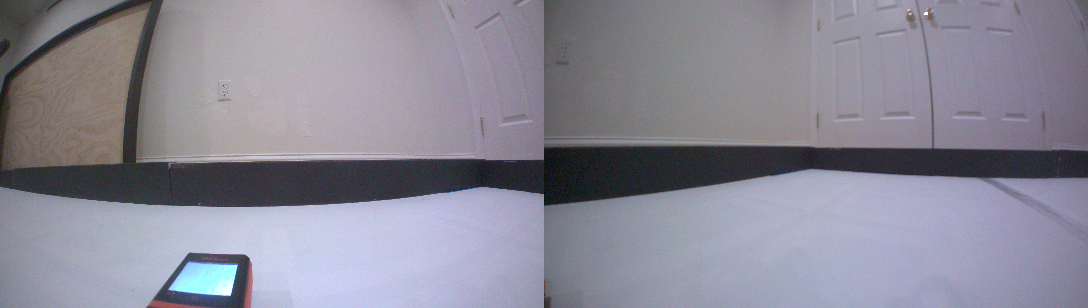
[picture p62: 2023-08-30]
dist/calibration/images/test3.png

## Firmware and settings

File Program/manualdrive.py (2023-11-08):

from IO import io
from Util import server
from Controller import controller as controller
from Controller import converter
import traceback
import cv2
import base64
import time
from threading import Thread
import sys

running = True
def main():
    global running
    try:
        io.setStatusBlink(0)
        acceptTerminalInput = True
        for i, arg in enumerate(sys.argv):
            if i != 0:
                if arg == 'no_terminal':
                    acceptTerminalInput = False
        server.open()
        controller.setMode(manual = True)
        io.setStatusBlink(2)
        quality = [int(cv2.IMWRITE_JPEG_QUALITY), 10]
        streaming = False
        predictStreaming = False
        def idManual(data):
            server.emit('idManual', 0)
        def drive(data):
            io.drive.throttle(data[0]['throttle'])
            io.drive.steer(data[0]['steering'])
        def capture(data):
            try:
                if data[0]['save'] == True:
                    if data[0]['colors'] != False:
                        converter.setColors(data[0]['colors'], True)
                    io.camera.capture(data[0]['filter'], data[0]['undistort'], True)
                else:
                    if data[0]['filter'] == True:
                        if data[0]['colors'] != False:
                            converter.setColors(data[0]['colors'], True)
                        if data[0]['undistort'] == True:
                            encoded = [
                                base64.b64encode(cv2.imencode('.png', cv2.merge(converter.filter(converter.undistort(io.camera.read()[0]))))[1]).decode(),
                                base64.b64encode(cv2.imencode('.png', cv2.merge(converter.filter(converter.undistort(io.camera.read()[1]))))[1]).decode(),
                                1,
                                0,
                                0
                            ]
                            server.emit('capture', encoded)
                        else:
                            encoded = [
                                base64.b64encode(cv2.imencode('.png', cv2.merge(converter.filter(io.camera.read()[0])))[1]).decode(),
                                base64.b64encode(cv2.imencode('.png', cv2.merge(converter.filter(io.camera.read()[1])))[1]).decode(),
                                1,
                                0,
                                0
                            ]
                            server.emit('capture', encoded)
                    else:
                        if data[0]['undistort'] == True:
                            encoded = [
                                base64.b64encode(cv2.imencode('.jpg', converter.undistort(io.camera.read()[0]), quality)[1]).decode(),
                                base64.b64encode(cv2.imencode('.jpg', converter.undistort(io.camera.read()[1]), quality)[1]).decode(),
                                0,
                                0,
                                0
                            ]
                            server.emit('capture', encoded)
                        else:
                            encoded = [
                                base64.b64encode(cv2.imencode('.jpg', io.camera.read()[0], quality)[1]).decode(),
                                base64.b64encode(cv2.imencode('.jpg', io.camera.read()[1], quality)[1]).decode(),
                                0,
                                0,
                                0
                            ]
                            server.emit('capture', encoded)
            except Exception as err:
                traceback.print_exc()
                io.error()
                server.emit('programError', str(err))
        def stream(data):
            nonlocal streaming
            streaming = not streaming
            if data[0]['save'] == True:
                if not streaming:
                    io.camera.stopSaveStream()
                else:
                    if data[0]['filter'] == True:
                        converter.setColors(data[0]['colors'], True)
                    io.camera.startSaveStream(data[0]['filter'], data[0]['undistort'], True)
            else:
                if not streaming:
                    io.camera.stopStream()
                else:
                    if data[0]['filter'] == True:
                        converter.setColors(data[0]['colors'], True)
                    io.camera.startStream(data[0]['filter'], data[0]['undistort'])
        def predictStream(data):
            nonlocal predictStreaming
            predictStreaming = not predictStreaming
            if predictStreaming:
                def loop():
                    nonlocal predictStreaming
                    try:
                        while predictStreaming:
                            start = time.time()
                            controller.drive()
                            time.sleep(max(0.1-(time.time()-start), 0))
                    except Exception as err:
                        traceback.print_exc()
                        io.error()
                        server.emit('programError', str(err))
                thread = Thread(target = loop)
                thread.start()
                server.emit('message', 'Began prediction stream')
                server.emit('predictStreamState', [True])
                print('Began prediction stream')
            else:
                server.emit('message', 'Ended prediction stream')
                server.emit('predictStreamState', [False])
                print('Ended prediction stream')
        def resetPrediction(data):
            controller.slam.carAngle = 0
        def getColors(data):
            server.emit('colors', converter.getColors())
        def setColors(data):
            converter.setColors(data[0], True)
        def getStreamState(data):
            nonlocal predictStreaming
            server.emit('streamState', io.camera.streamState())
            server.emit('predictStreamState', [predictStreaming])
        server.on('idManual', idManual)
        server.on('drive', drive)
        server.on('capture', capture)
        server.on('stream', stream)
        server.on('predictStream', predictStream)
        server.on('resetPrediction', resetPrediction)
        server.on('getColors', getColors)
        server.on('setColors', setColors)
        server.on('getStreamState', getStreamState)
        global running
        running = True
        def stop(data):
            global running
            running = False
            print('\n STOPPING PROGRAM. DO NOT INTERRUPT.')
            io.close()
            server.close()
            sys.exit(0)
        io.imu.setAngle(0)
        server.on('stop', stop)
        acceptTerminalInput = False
        if acceptTerminalInput:
            while running:
                msg = input()
                if msg == 'reset':
                    server.emit('colors', converter.setDefaultColors())
                elif msg == 'calibrate-gyro':
                    io.imu.calibrate()
                elif msg == 'stop':
                    break
                elif msg != '':
                    server.emit('unsafemessage', msg)
        else:
            while running:
                time.sleep(1)
    except KeyboardInterrupt:
        print('\nSTOPPING PROGRAM. DO NOT INTERRUPT.')
    except Exception as err:
        print('---------------------- AN ERROR OCCURED ----------------------')
        traceback.print_exc()
        io.error()
        server.emit('programError', str(err))
    running = False
    io.close()
    server.close()
    sys.exit(0)

if __name__ == '__main__':
    main()

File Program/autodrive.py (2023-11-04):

from IO import io
from Util import server
from Controller import controller as controller
import time
import sys
import traceback
running = True
actuallyRunning = True

def main():
    global running, actuallyRunning
    try:
        io.setStatusBlink(0)
        infinite = False
        wait = False
        sendServer = True
        for i, arg in enumerate(sys.argv):
            if i != 0:
                if arg == 'infinite':
                    infinite = True
                if arg == 'wait_for_button':
                    wait = True
                if arg == 'no_server':
                    sendServer = False
        if infinite:
            print('PROGRAM RUNNING IN INFINITE MODE!')
        if sendServer:
            server.open()
            controller.setMode(sendServer=True)
        else:
            controller.setMode(sendServer=False)
        io.setStatusBlink(1)
        if wait:
            print('Waiting for button')
            io.waitForButton()
        else:
            time.sleep(1)
        io.setStatusBlink(2)
        def stop(data):
            global actuallyRunning
            actuallyRunning = False
            print('Stopped by stop button')
            io.setStatusBlink(0)
            io.close()
            server.close()
            sys.exit(0)
        server.on('stop', stop)
        io.drive.throttle(controller.speed)
        io.imu.setAngle(0)
        print("starting run")
        while running and actuallyRunning:
            running = controller.drive()
            if infinite: running = True
        print('Stopped by driver command')
    except KeyboardInterrupt:
        print('\nSTOPPING PROGRAM. DO NOT INTERRUPT.')
    except Exception as err:
        print('---------------------- AN ERROR OCCURED ----------------------')
        traceback.print_exc()
        io.error()
        server.emit('programError', str(err))
    running = False
    io.drive.throttle(0)
    io.close()
    server.close()
    sys.exit(0)

if __name__ == '__main__':
    main()

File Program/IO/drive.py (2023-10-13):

from IO import io
from Util import server
from adafruit_servokit import ServoKit
import busio
import board
from threading import Thread
import time
import traceback

# drive module that does driving stuff

__pwm = ServoKit(channels = 16, i2c = busio.I2C(board.SCL_1, board.SDA_1))

__currThr = 0
__targetStr = 0
__currStr = 0
__throttleFwd = 0.08
__throttleRev = -0.15
__steeringCenter = 90
__steeringRange = 45
__steeringTrim = 12
__steeringMaxDiff = 40
__thread = None
__running = True
def __update():
    global __currStr, __targetStr, __steeringCenter, __steeringRange, __steeringTrim, __pwm, __running, __steeringMaxDiff
    try:
        lastAngle = 0
        while __running:
            # __currStr = (__smoothFactor * __currStr) + ((1 - __smoothFactor) * __targetStr)
            __currStr += max(-__steeringMaxDiff, min(__steeringMaxDiff, __targetStr - __currStr))
            angle = round((__currStr * __steeringRange / 100) + __steeringCenter + __steeringTrim)
            if angle != lastAngle: __pwm.servo[1].angle = angle
            lastAngle = angle
            time.sleep(0.02)
    except Exception as err:
        traceback.print_exc()
        io.error()
        server.emit('programError', str(err))
def steer(str: int):
    global __targetStr
    __targetStr = max(-100, min(str, 100))
def throttle(thr: int):
    global __pwm, __currThr, __throttleFwd, __throttleRev
    __currThr = max(-100, min(thr, 100))
    if (__currThr < 0):__pwm.continuous_servo[0].throttle = (__currThr / 100) * (-__throttleRev) + 0.1
    else: __pwm.continuous_servo[0].throttle = (__currThr / 100) * __throttleFwd + 0.1
def trim(trim: int):
    global __steeringTrim
    __steeringTrim = trim
    steer(__currStr)
def setMaxSteerDiff(diff: float):
    global __steeringMaxDiff
    __steeringMaxDiff = max(0, min(diff, 1))

def currentSteering():
    global __currStr
    return __currStr
def getMaxSteerDiff():
    global __steeringMaxDiff
    return __steeringMaxDiff

def stop():
    global __running
    steer(0)
    throttle(0)
    __running = False
    __thread.join()

__thread = Thread(target = __update)
__thread.start()
steer(0)
throttle(0)

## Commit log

2023-05-07 update parts list/create Assembly.md stub
2023-05-28 add CAD models
    [SPARK-G2-cablecover.stl, SPARK-G2-chassis-base.stl, SPARK-G2-steeringtower-bottom.stl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]
2023-05-30 add more CAD files + cleanup stuff
    [SPARK-G2-chassis-platform.stl, SPARK-G2-chassis-upperplatform.stl]
2023-06-11 more CAD files
    [SPARK-G2-cameratower-carrier.stl, SPARK-G2-cameratower-rail.stl, SPARK-G2-chassis-base.stl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]
2023-06-24 Update CAD files to v1.2
    [SPARK-G2-antennamount.stl, SPARK-G2-cablecover.stl, SPARK-G2-steeringtierod-left.stl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]
2023-06-26 actually update to v1.2
    [SPARK-G2-cablecover.stl, SPARK-G2-chassis-base.stl, SPARK-G2-chassis-platform.stl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]
2023-06-28 fix voltage meter clearance issues
    [SPARK-G2-voltmeterbracket-1.stl, SPARK-G2-voltmeterbracket-2.stl]
2023-06-29 update to sort of work on 2023 build
    [SPARK-G2-antennamount.stl]
2023-07-02 as的发射点发我个
2023-07-02 add IMU placeholder
2023-07-04 Revert "fix"
    This reverts commit 64532894c91a66bfa5cd024b41157b5b7084ca56.
    [camera.py]
2023-07-04 Revert "Revert "fix""
    This reverts commit c8fe4e8952f172fb2dae2e757dc6bd16d2dc0ea3.
    [camera.py]
2023-07-04 Revert "Revert "Revert "fix"""
    This reverts commit 3290df46d70d4146b95a96915eb69f693a3414f4.
    [camera.py]
2023-07-04 fix io and camera crashes
    [camera.py, io.py, manualdrive.py]
2023-07-04 actually fix the camera crash
    [camera.py]
2023-07-06 update CAD to v1.3
    [SPARK-G2-chassis-base.stl, SPARK-G2-chassis-platform.stl, SPARK-G2-dustcover-left.stl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]
2023-07-08 fix web server CORS issue
    [camera.py, manualdrive.py]
2023-07-08 update CAD to v1.3-1
    [SPARK-G2-chassis-base.stl, SPARK-G2-frontcover.stl]
2023-07-08 implement python server
    probably still broken
    [autodrive.py, camera.py, manualdrive.py]
2023-07-08 奥尔森非法手段更丰富
2023-07-08 fix server i guess
    [io.py, manualdrive.py]
2023-07-08 move stream code + fix server more
    [camera.py, io.py, manualdrive.py]
2023-07-08 update CAD models to v1.3 again
    [SPARK-G2-cameratower-carrier.stl]
2023-07-09 add flags for encoding + ping cross-connection fix
    [camera.py, manualdrive.py]
2023-07-09 add history slider frame
2023-07-10 button auto resize into slideout
2023-07-11 fix some of the server stuff
    [manualdrive.py]
2023-07-11 fix stream state bug
    [manualdrive.py]
2023-07-11 add camera control butons
2023-07-11 fix capture filter error
    [camera.py]
2023-07-13 error reporting from server
    [camera.py]
2023-07-13 calibration sucks
2023-07-13 separate filter/save modifiers
2023-07-13 fix filter crash + better error tracing
    [camera.py, manualdrive.py]
2023-07-13 change ordering of converter.filter output
2023-07-13 import/export buttons
2023-07-14 add gyro code
2023-07-14 push camera fix
    camera has been fixed
    as well as converter
    pushed instant crash fix also
2023-07-18 camera.py create output dir if doesn't exist
    [camera.py, manualdrive.py]
2023-07-18 implement gyro into slam.py
2023-07-18 fix steering
2023-07-18 distortion so bork
    [SPARK-G2-steeringtower-top.stl, SPARK-G2-steeringtower-topleft.stl, SPARK-G2-steeringtower-topright.stl]
2023-07-18 switch to custom NVCamera
2023-07-19 Add undistortion calibration and fix
2023-07-20 fix controller on control panel
    [drive.py]
2023-07-20 Add driver code, fix pillar storage
2023-07-20 disable camera auto exposure/auto white balance
    why is it so dark
2023-07-20 move calibration + remove unused images
2023-07-20 fix calibrate
2023-07-20 sound fix/ crash fix / idk
    [manualdrive.py]
2023-07-21 fix driver
2023-07-21 wall heights are very wrong
    [io.py]
2023-07-22 Most Useless Fix Ever (MUFE)
    [autodrive.py]
2023-07-23 add download frame button
2023-07-23 fix control panel raw landmark errors
    [manualdrive.py]
2023-07-23 use gyro
2023-07-24 fix control panel car angle + imu type annotation
    [imu.py]
2023-07-24 aa fix bugs and calirbrate gyro
    [imu.py, manualdrive.py]
2023-07-24 add steering smoothing
2023-07-24 oops ufnction name wrong
    [drive.py]
2023-07-25 add steering display
2023-07-25 Revert "use gyro"
2023-07-25 Revert "Revert "use gyro""
    This reverts commit 8a3e6c609e3665c247ed890f18314ca1b95321e3.
2023-07-25 fix backward steering display
2023-07-26 fix assembly
2023-07-27 reMOOve prints
2023-07-27 FIX RUN ON STARTUP
    [camera.py, imu.py, io.py]
2023-07-27 fix camera shake and delete dont click this this
2023-07-28 fix camera calibration documentation
2023-07-28 move 3d models to /dist/
    [SPARK-G2-antennamount.stl, SPARK-G2-cablecover.stl, SPARK-G2-cameratower-carrier.stl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]
2023-07-28 reduce servo lag
2023-07-28 fix filter
2023-07-30 fix filter for official mat, tune values
2023-08-05 fix server fail when run on startup disabled
    [startup.py]
2023-08-05 fix program stop not stopping
    [drive.py]
2023-08-15 fix self-xss
    self-xss isn't even xss
    [manualdrive.py]
2023-08-22 fix camera
2023-08-30 fix dumb typo of incorrectness
    [camera.py]
2023-08-30 add filtered image
2023-08-31 fix typo and add predict button
2023-08-31 add styles + code for predict button lol
    oops
2023-09-05 mvoe disconnect button code out of random function
2023-09-17 increase max steering lock
2023-09-18 add run buttons that are very borken
    don't spam them because it'll just keep running them
2023-09-23 fix program not exit probably
    [autodrive.py, manualdrive.py]
2023-09-23 fix program not exiting
    [manualdrive.py]
2023-09-25 fix bugs and servo is borked
    [drive.py]
2023-09-28 buh servo is fixed
    [manualdrive.py]
2023-09-30 fix idmanual and steering trim and print spam
    [drive.py, manualdrive.py]
2023-09-30 clean up and fix control panel map
    [imu.py]
2023-10-01 fix leftover code bugs
    [manualdrive.py]
2023-10-02 fix formatting stuff also gyro print spam
    [manualdrive.py]
2023-10-12 fix bugs and add servoSpammer.py
2023-10-13 change steering smoothing to linear function
2023-10-22 more documentation!!
    [SPARK-G2-antennamount.stl, SPARK-G2-cablecover.stl, SPARK-G2-cameratower-carrier.stl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]
2023-11-03 fix calibration
2023-11-04 add wiring diagram
2023-11-04 fix wiring diagram
    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
2023-11-05 fix wiring diagram I2C color
2023-11-05 add SPARK-Calibrator
2023-11-05 add SPARK Calibrator to documentation
2023-11-05 add undistort option and fix calibrator
    [manualdrive.py]
2023-11-05 add undistort option to everything but its probably borken and will crash instantly
    [camera.py, manualdrive.py]
2023-11-05 fix randomiser, add gyro spammer, fix controller
2023-11-07 fix crash with streaming
    [camera.py, manualdrive.py]
2023-11-07 initial calibration for internat\ionals
